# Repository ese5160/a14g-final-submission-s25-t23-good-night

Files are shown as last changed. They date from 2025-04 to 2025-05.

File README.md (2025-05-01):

Review Assignment Due Date (https://classroom.github.com/a/AlBFWSQg)
# a14g-final-submission

    * Team Number: T23
    * Team Name: Good Night
    * Team Members: Haichao Zhao, Zeng Li
    * Github Repository URL: https://github.com/ese5160/a14g-final-submission-s25-t23-good-night
    * Description of test hardware: (development boards, sensors, actuators, laptop + OS, etc) SAMW25, laptop

## 1. Video Presentation

The link to video presentation: [Video Presentation](https://drive.google.com/file/d/199g08DGVsTHXfeQyzWboZk-IfXS3VhQH/view?usp=sharing)

## 2. Project Summary

- Device Description

> We designed a desk electronic car with multiple functions to entertain users within boring working days. It can be controlled by anyone's voice command and task buttons in the web UI.

> What inspired you to do the project? What problem is your device solving?
>> In our daily life, we usually have to sit in the front of desks for multiple hours and sometimes we need to take a break and have some entertainment to make our life more interesting.
>
>> So in order to provide some ways to relax, we designed this desk electronic car. It will accompany with you and interact with you via your voice. Moreover, it can remaind you to take a break by showing LCD animation and led show. Users can play with it to command it to move around.

> How do you use the Internet to augment your device functionality?
>> We use Claude and chatGPT to give us some advice about chip selection and create some helpful code library.

- Device Functionality

> We use WINC1500 chip to do wifi connection and communicate with our MCU. In order to download firmware over the air, we created a virtual machine and uplode our new firmware. MCU can connect to wifi via wifi module and download the new firmware in the VM website and store it in the bootloader. Besides, we use node-red to remotely control our device via MQTT protocal.

> **Sensors:**
>> IMU
>>
>> Microphone
> 
> **Actuators:**
>> LCD
>>
>> Speaker
>>
>> Motor
>
> **Other modules:**
>> 5V module

> Block diagram
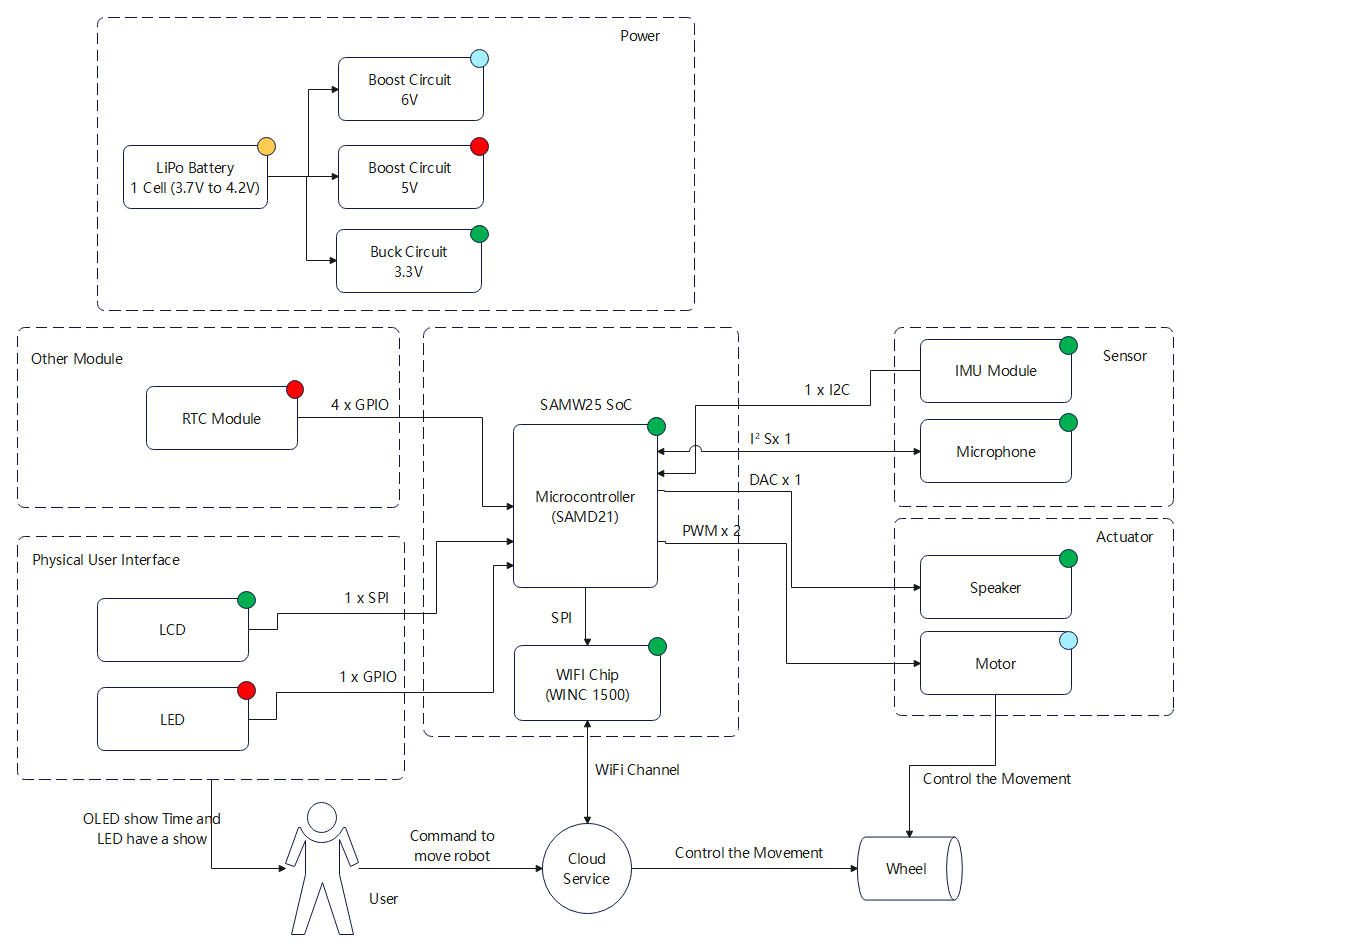
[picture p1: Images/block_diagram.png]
block diagram
> 

- Challenges

> The first great challenge we met is about our 5V power module in our PCBA. The output voltage of 5V module was near 0. So in the end, we chose to desolder the jumpers for the 5V boost and used an individual 5V module and it works.
>
> The second challenge was we connected VSUB net with 5V net directly, which might lead to 5V power supply conflict. So in order to avoid this potential issue, we cut off the copper trace in the PCBA and using fly wire to reconnect the pins between our FTDI chip and power regulator chip. But soldering the fly wires was realy a time-cost and painful process. Luckily, we finished that.
>
> The third challenge is to integrate our individual functions together in FreeRTOS. During the integration process, we found count down time function and health remainder function had a serious conflict and wifi task needed a vary large heap to run successfully. After one whole day debugging, we still cannot integrate the count down time and health remainder together. So we had to give up the count down time function. For the wifi heap allocation, we tried to give smaller heap for each task and give more heap space for wifi. And ultimately, it works.

- Prototype Learnings

> The lessons I have learned from building and testing our prototype:
>> Firstly, deviding VUSB net from 5V boost output net.
>>
>> Secondly, always double even trible check the components to make sure their standard running voltage and current and power.
>>
>> Thirdly, when choosing LED strip, I need to figure out whether the MCU can provide the clock freqency required by the LED strip.

> What would you do differently if you had to build this device again?
> 
> I will definitely check my key components standard working condition such as inductors used for power regulator. And split the VUSB with 5V net.
 
- Next Steps & Takeaways

> What steps are needed to finish or improve this project?
>> We need to improve our UI display to show IMU data and configure our RTC initial time via Node-Red rather than software setup. Beside we need to add a distance sensor to detect the surrounding item in order to avoid falling from high altitude.

> What did you learn in ESE5160 through the lectures, assignments, and this course-long prototyping project?
>> Lots of things, including:
>> - Altium Designer using
>> - The procedure of PCBA designing
>> - PCBA test procedure
>> - Advanced soldering skills
>> - Professional device using: scrimper, e-load, temperature test gun, etc.
>> - MQTT based IOT controlling.
>> - Node-Red using
>> - OTAFU implementing
>> - FreeRTOS utilizing
>> - etc

- Project Links
> [URL to your Node-RED instance for our review ](http://172.177.231.136:1880/ui/#!/0?socketid=XXV4ffUuj0cg4lLcAAEU)

> [The share link to your final PCBA on Altium 365.](https://upenn-eselabs.365.altium.com/designs/7828C69B-F65F-46A7-A406-FC1A5B1ED7EE)

## 3. Hardware & Software Requirements

**Pass**:

- [√] Design Review Criteria

**Fail**:

- [ ] Design Review Criteria

### For Hardware Requirements

- [√] Project shall be based on SAMW25 microcontroller.

- [√] A 39x41x3.3mm OLED shall be used as user interface.

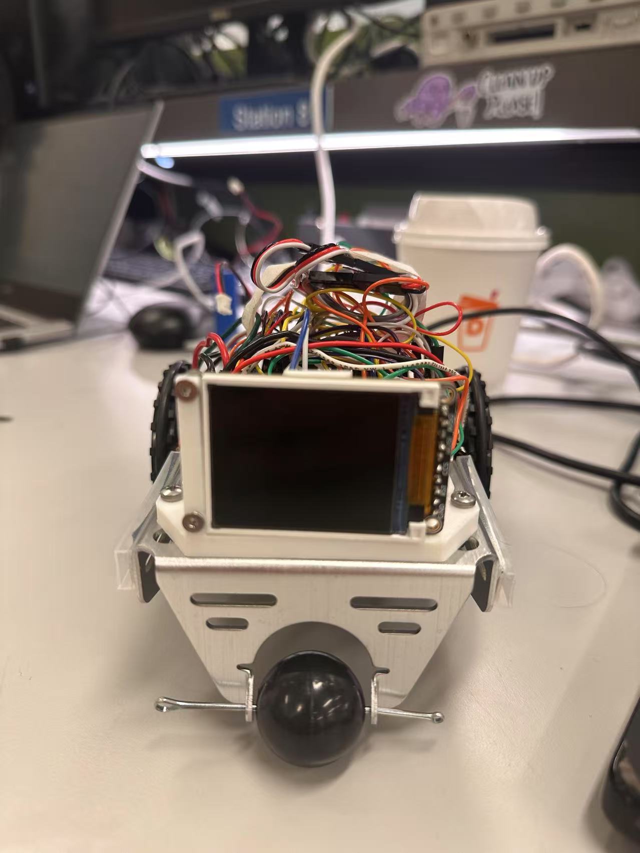
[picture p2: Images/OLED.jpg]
OLED


- [√] The Electronic Pet shall move around with wheels controlled by PWM signals(≥20kHz frequency).

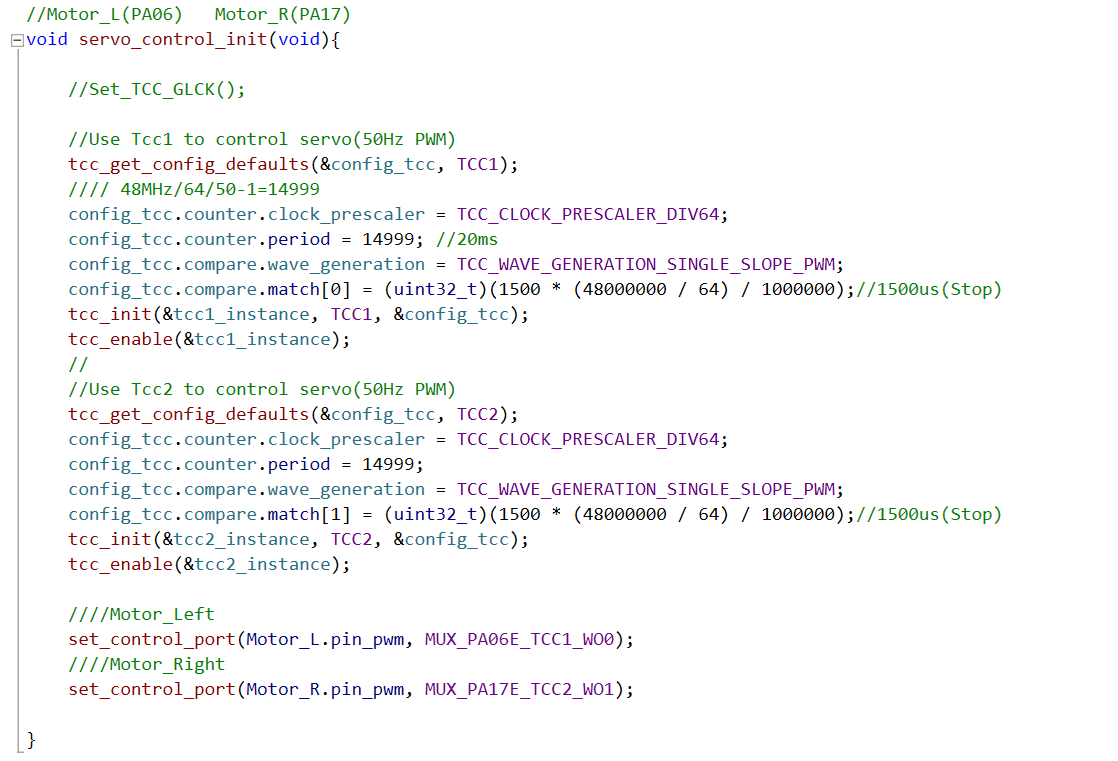
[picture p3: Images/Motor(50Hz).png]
PWM Signals


- [√] The project shall utilize a microphone to capture users' voice command.

[Voice Command](https://drive.google.com/file/d/1vsd7IJbTeATzNU7q7ol-T68C_iqhJChO/view?usp=sharing)

- [√] The project shall utilize a speaker to play audio signals.

[Audio Signals](https://drive.google.com/file/d/1vsd7IJbTeATzNU7q7ol-T68C_iqhJChO/view?usp=sharing)

- [√] The Electronic Pet shall have colorful lightning effect by using led strips based on I/O pins sending color data.

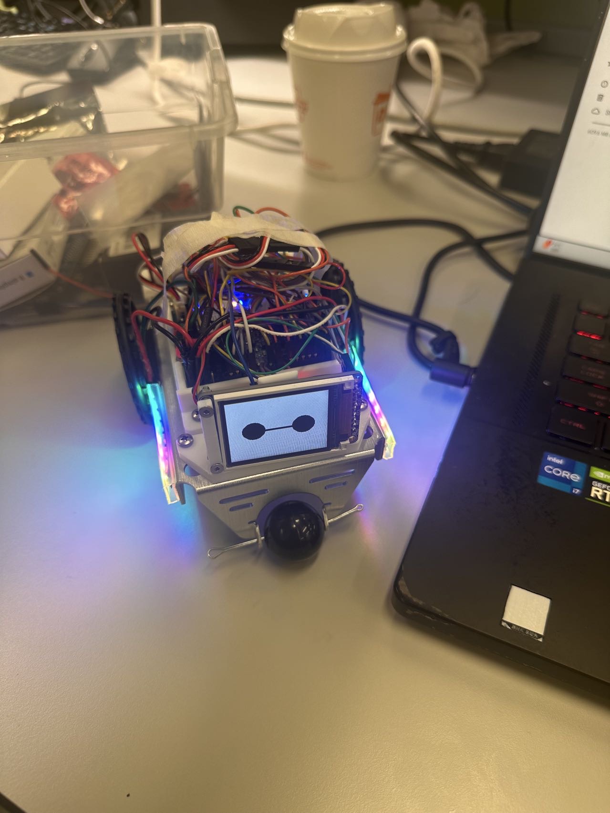
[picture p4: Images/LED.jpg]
LED Strip


- [√] The Electronic Pet shall using 1-cell Li-Po battery with normal voltage 3.7V to power itself.

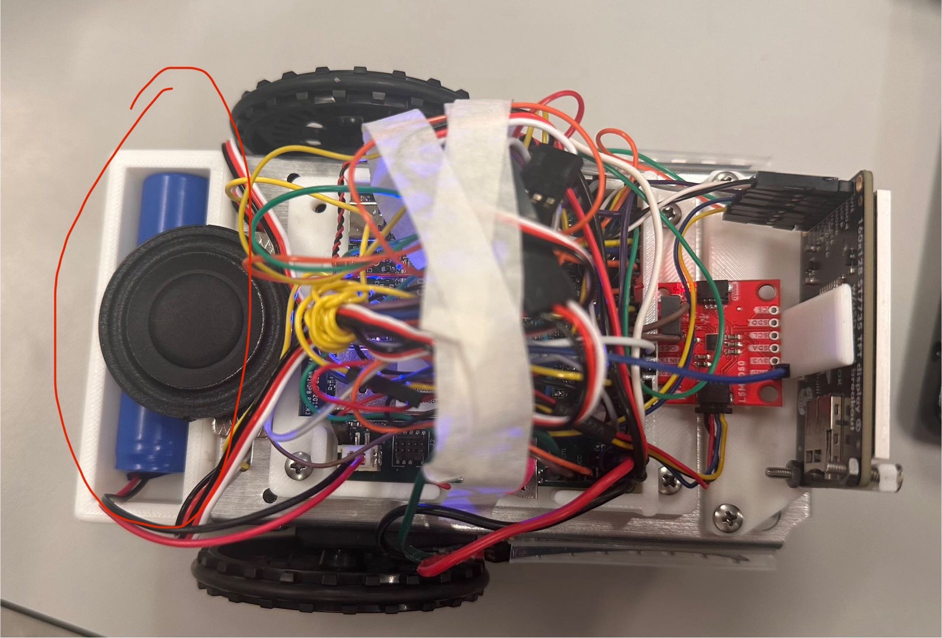
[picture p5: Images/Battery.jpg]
Battery


- [ ] The Elctronic Pet shall have a hardware audio weak-up button to activate voice detection functionality.

(But for this one, we can weak-up audio by using voice command)

[Voice Weak-up](https://drive.google.com/file/d/1QjdPzAFBdYn6xlC-yM1D15jq5Nro2u9h/view?usp=drive_link)

- [√] The Elctronic Pet shall have a switch to allow firmware downloaded between MCU and AI voice module.

- [√] The Elctronic Pet shall have a reset button to reset MCU.

### For Software Requirements

- [√] The OLED shall show real time clock with time changing animation under idle mode.

[Real Time Clock](https://drive.google.com/file/d/113563IdeDLPqgcDlNYIJI8t_Kfd6H3IC/view?usp=sharing)

- [√] The Electronic Pet shall count down time, set by users' voice command(all voice ommand response time ≤100ms and all voice recognition accuracy ≥95%).

[Voice Control](https://drive.google.com/file/d/1uEhCCXdXMqlJPuAjUW_ZJtCygNJ_ypcy/view?usp=drive_link)

- [√] The OLED shall show time counting down changing animation.

[Count Down Time](https://drive.google.com/file/d/1uEhCCXdXMqlJPuAjUW_ZJtCygNJ_ypcy/view?usp=drive_link)

- [√] The project shall control LED strip to display several modes: blinking with one color in 0.5 milisecond period, holding in one color, holding in multiple colors.

[Led Modes](https://drive.google.com/file/d/1Ynfru8uWko6rZNohwsRf4ItYq9wje_we/view?usp=drive_link)

- [√] The Electronic Pet shall move forward, move backward, turn left and turn right based on users' voice command or mobile application control.

[Motor Control Based on Node-RED](https://drive.google.com/file/d/1fZCSuxt042b5PfyyEALYGmumLY5jCH-g/view?usp=sharing)

[Motor Control Based on Voice Module](https://drive.google.com/file/d/1cLYKxjtBCbKXMLHO_yQR-n1LWBqkUQFy/view?usp=sharing)

- [√] The Electronic Pet shall remind users to take breaks (OLED displaying animation for 10 seconds) and play a light show when 30 minutes counting down ends. (For test, we set time to 60 seconds)

[Health Reminder](https://drive.google.com/file/d/1pByXs5zT0Y9-n48iyKIn96K74kvmEg7N/view?usp=sharing)

- [√] The Electronic Pet shall recognize and answer users' voice commands in 3 seconds after recieving voice activation commands.

[Voice Command Answer in 3 seconds](https://drive.google.com/file/d/1vsd7IJbTeATzNU7q7ol-T68C_iqhJChO/view?usp=sharing)

- [√] The OLED display shall communicate with MCU via SPI bus(≥10MHz) and display refresh rate ≥30fps.

- [√] The microphone shall send signals to AI module via I2S bus(Audio sampling rate ≥44.1kHz).

- [√] The speaker shall communicate with AI module via PWM/DAC signals.

## 4. Project Photos & Screenshots

- Final project, including any casework or interfacing elements that make up the full project (3D prints, screens, buttons, etc)

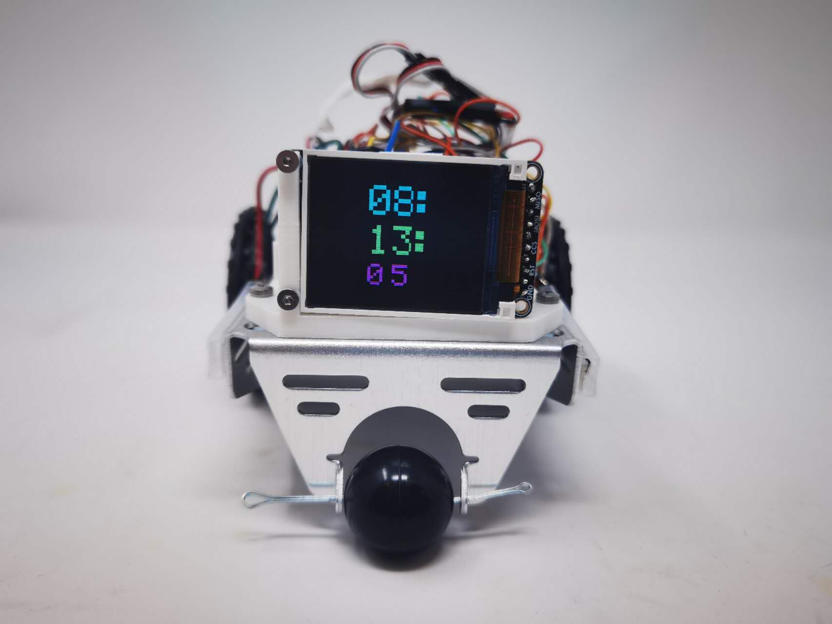
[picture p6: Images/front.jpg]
front

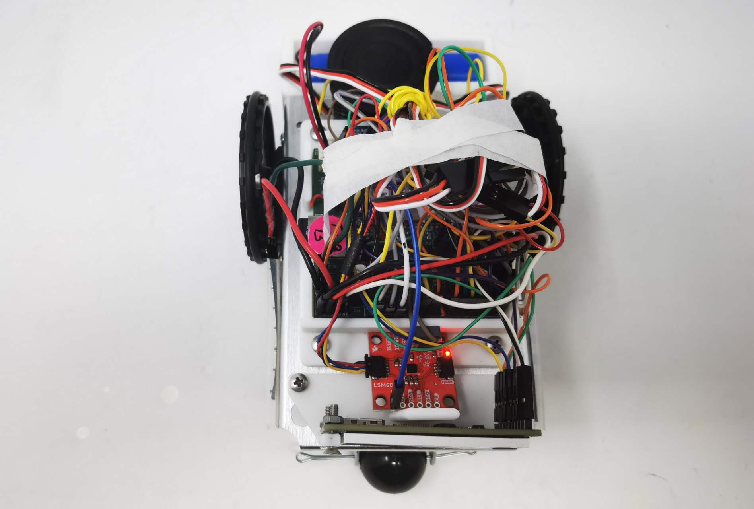
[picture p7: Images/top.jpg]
top

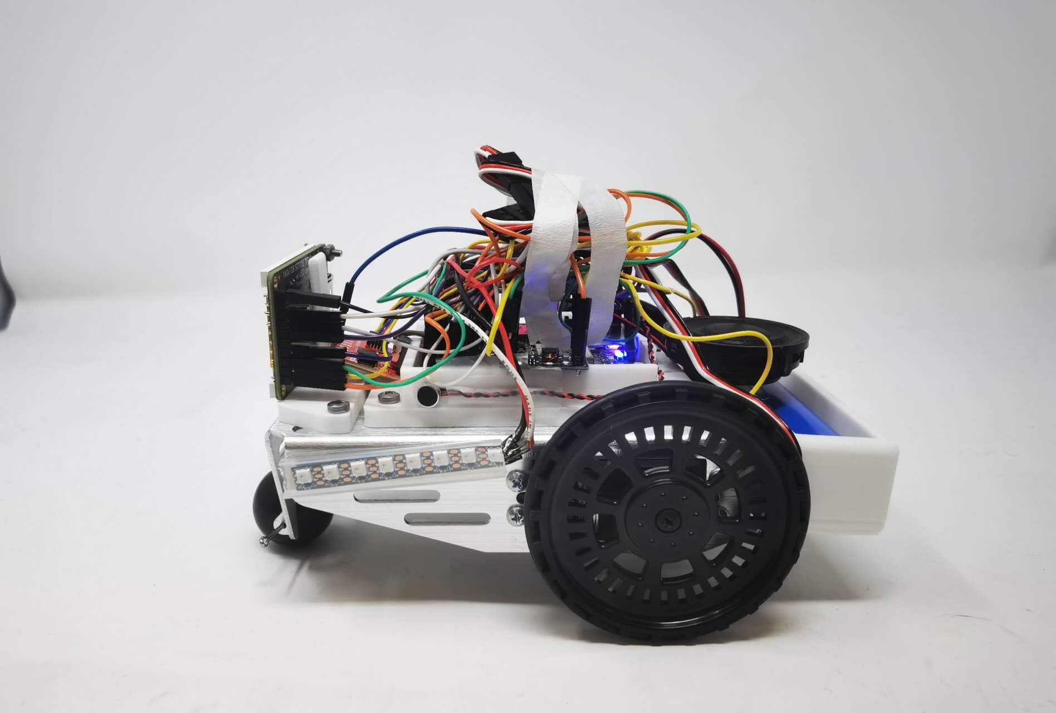
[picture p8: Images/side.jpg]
side

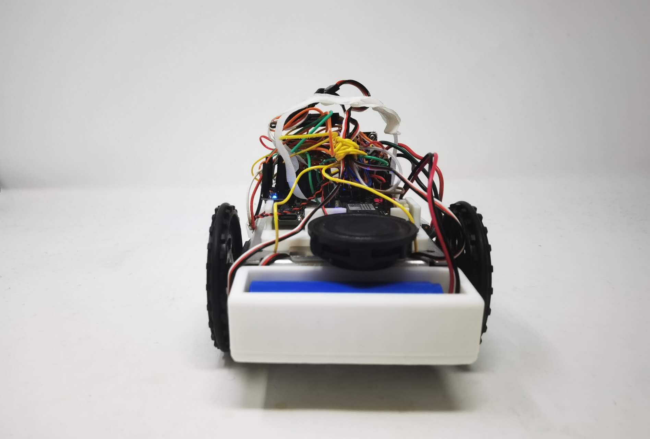
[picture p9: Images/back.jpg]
back

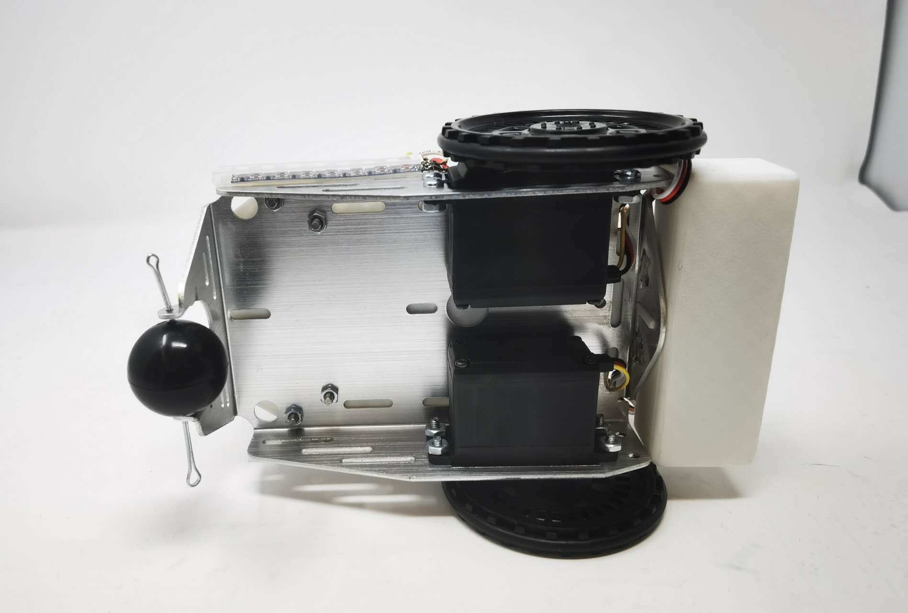
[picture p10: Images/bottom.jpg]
bottom


- The standalone PCBA, top
The standalone PCBA, top
- The standalone PCBA, bottom
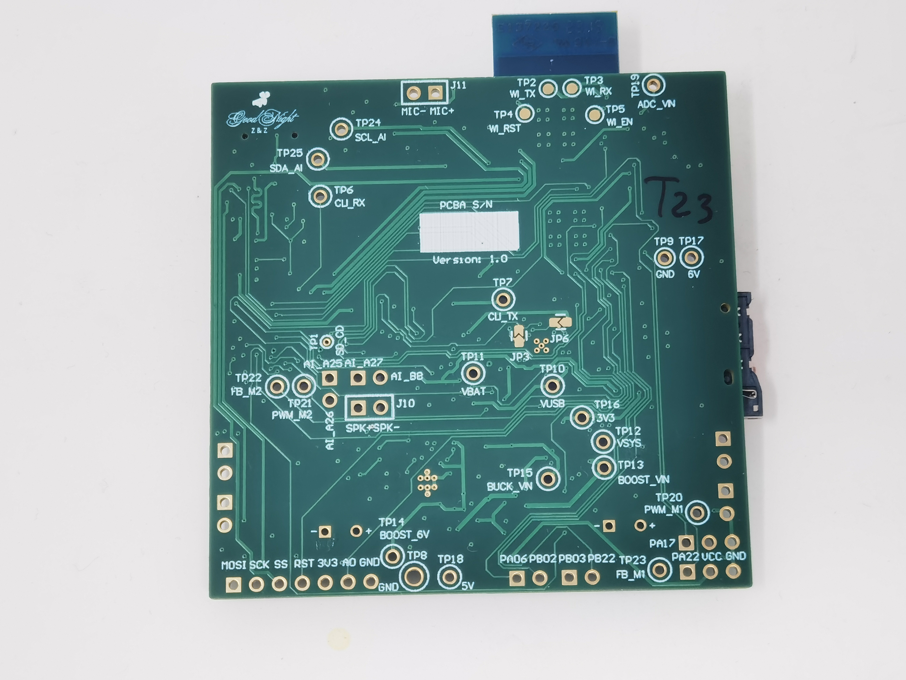
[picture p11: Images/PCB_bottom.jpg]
The standalone PCBA, bottom

- Thermal camera images while the board is running under load 
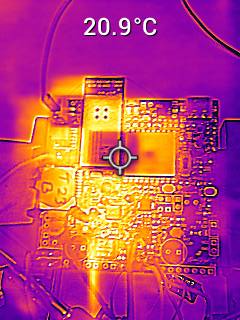
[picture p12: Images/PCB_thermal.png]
Thermal camera images

- The Altium Board design in 2D view (screenshot)
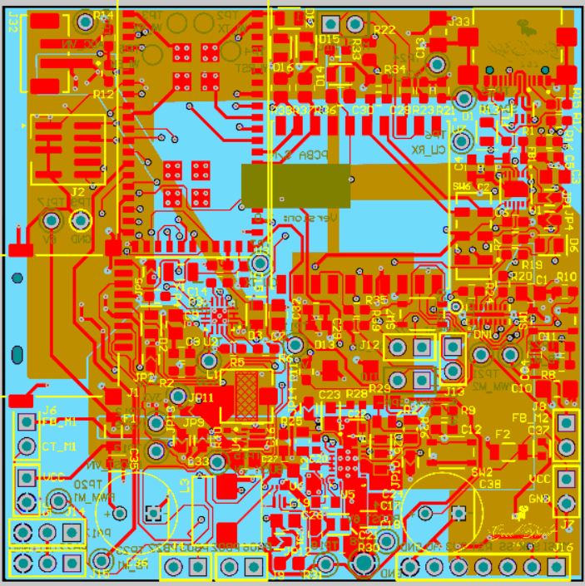
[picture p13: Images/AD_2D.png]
AD_2D

- The Altium Board design in 3D view (screenshot)
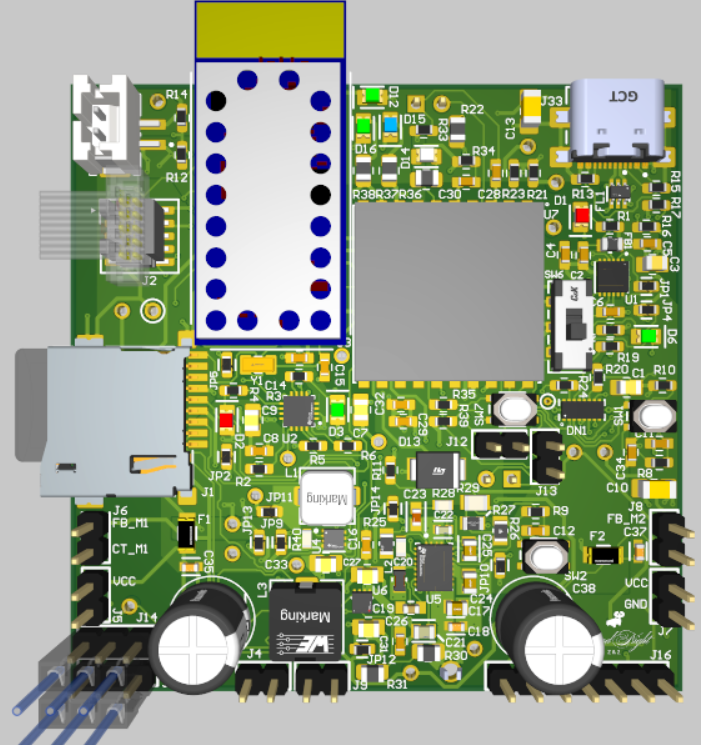
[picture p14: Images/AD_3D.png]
AD_3D

- Node-RED dashboard (screenshot)
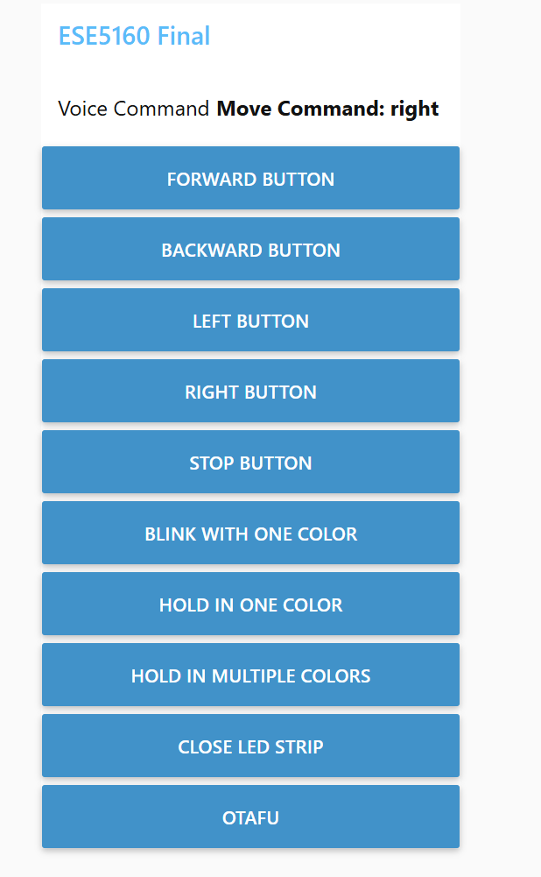
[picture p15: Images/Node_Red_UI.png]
UI

- Node-RED backend (screenshot)
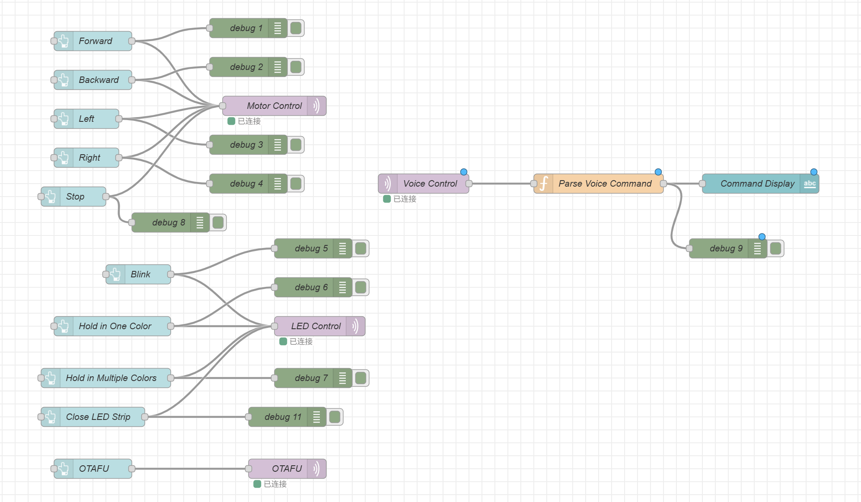
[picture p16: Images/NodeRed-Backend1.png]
backend_1

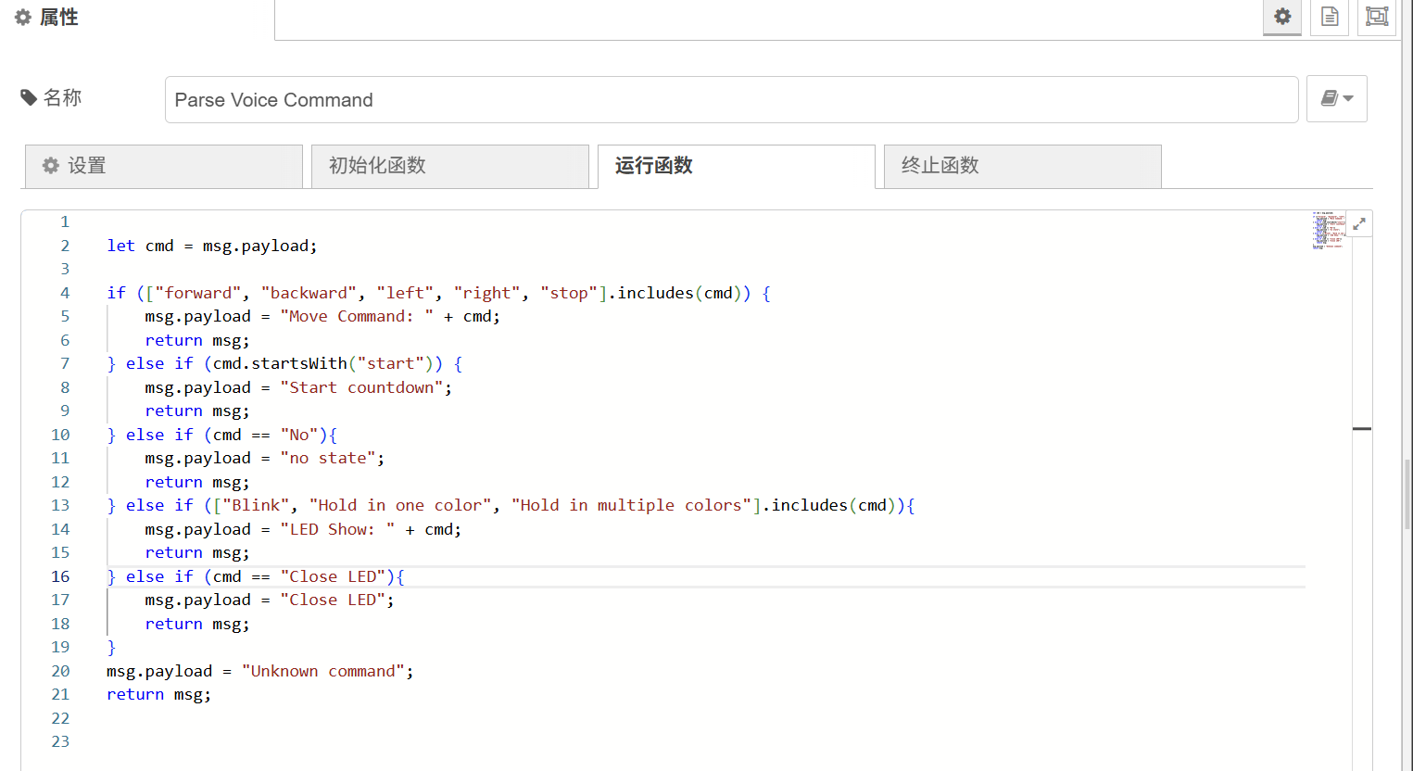
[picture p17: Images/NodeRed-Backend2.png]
backend_2

- Block diagram of your system
block diagram

## Codebase

- [Link to our final embedded C application firmware codebases](https://github.com/ese5160/a14g-final-submission-s25-t23-good-night/tree/main/Application)

- [Link to our final embedded C bootloader firmware codebases](https://github.com/ese5160/a14g-final-submission-s25-t23-good-night/tree/main/Bootloader)

- [Link to our AI voice module code](uni_hb_m_solution.zip)

- [Link to our Node-RED dashboard code](node_red.json)

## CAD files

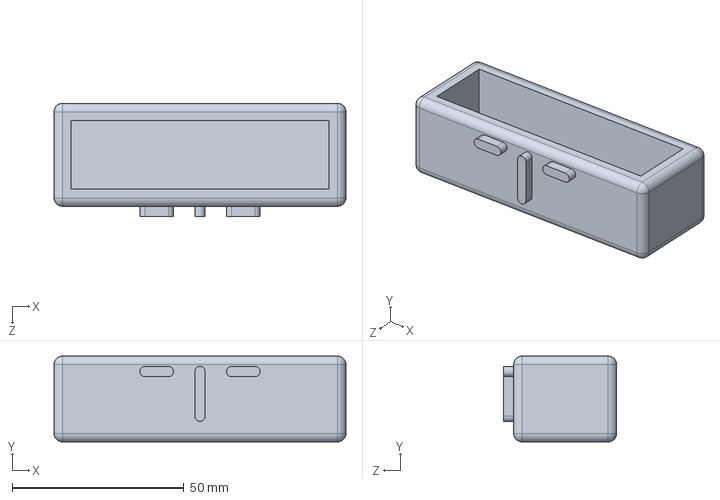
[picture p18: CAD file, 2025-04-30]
3D_Model/battery_cage.SLDPRT
85.0 x 25.0 x 33.0 mm

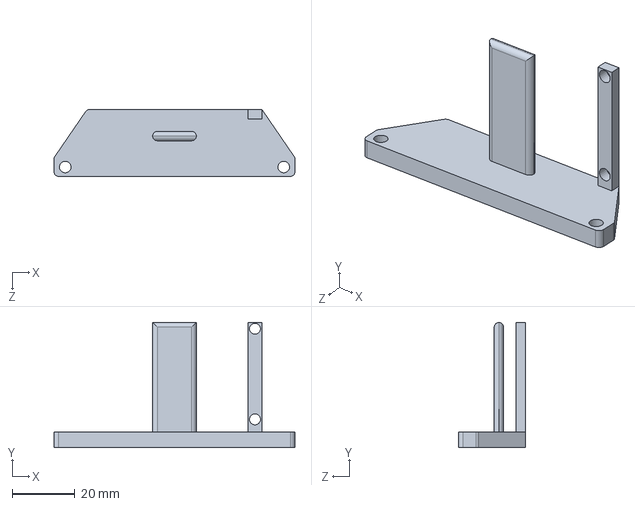
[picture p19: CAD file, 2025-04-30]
3D_Model/LCD_base.SLDPRT
77.1 x 40.0 x 21.4 mm

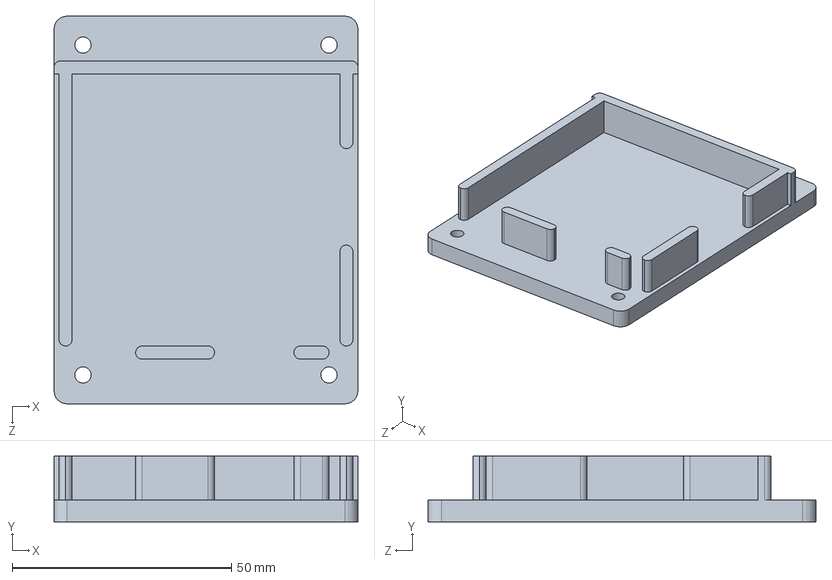
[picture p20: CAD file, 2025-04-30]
3D_Model/base.SLDPRT
69.3 x 15.0 x 88.4 mm

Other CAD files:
3D_Model/LCD_base.STL
3D_Model/base.STL
3D_Model/battery_cage.STL

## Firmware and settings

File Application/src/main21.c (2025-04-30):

/**
 * @file      main.c
 * @brief     Main application entry point
 * @author    Eduardo Garcia
 * @author    Nick M-G
 * @date      2022-04-14
 ******************************************************************************/

/****
 * Includes
 ******************************************************************************/
#include <errno.h>

#include "CliThread/CliThread.h"
#include "FreeRTOS.h"
#include "I2cDriver\I2cDriver.h"
#include "SerialConsole.h"
#include "WifiHandlerThread/WifiHandler.h"
#include "asf.h"
#include "driver/include/m2m_wifi.h"
#include "main.h"
#include "stdio_serial.h"

#include "Motor.h"
#include "LCD/LCD.h"
#include "RTC_LCD/rtc_lcd.h"
#include "LED/LED.h"
#include "Health_Reminder/Health_Reminder.h"
#include "AI_voice_control/voice_control.h"
#include "IMU/lsm6dso_reg.h"
#include "IMU/ImuTask.h"

#include "flag.h"

/****
 * Defines and Types
 ******************************************************************************/
#define APP_TASK_ID 0 /**< @brief ID for the application task */
#define CLI_TASK_ID 1 /**< @brief ID for the command line interface task */
#define WAIT_TX_COMPLETE_MS 1000

/****
 * Local Function Declaration
 ******************************************************************************/
void vApplicationIdleHook(void);
//!< Initial task used to initialize HW before other tasks are initialized
static void StartTasks(void);
void vApplicationDaemonTaskStartupHook(void);

void vApplicationStackOverflowHook(void);
void vApplicationMallocFailedHook(void);
void vApplicationTickHook(void);

/****
 * Variables
 ******************************************************************************/
static TaskHandle_t cliTaskHandle = NULL;       //!< CLI task handle
static TaskHandle_t daemonTaskHandle = NULL;    //!< Daemon task handle
static TaskHandle_t wifiTaskHandle = NULL;      //!< Wifi task handle
static TaskHandle_t uiTaskHandle = NULL;        //!< UI task handle
static TaskHandle_t controlTaskHandle = NULL;   //!< Control task handle
static TaskHandle_t healthTaskHandle = NULL;    //!< Health Monitor task handle
static TaskHandle_t lcdTaskHandle = NULL;		//!< LCD task handle
static TaskHandle_t ledTaskHandle = NULL;		//!< LED task handle
static TaskHandle_t voicecontrolTaskHandle = NULL;//!< Voice Control task Handle
static TaskHandle_t imuTaskHandle = NULL;

char bufferPrint[64];   ///< Buffer for daemon task

SystemState system_state = counting_down;

SemaphoreHandle_t xHealthMonitorSemaphore = NULL; // For Health Monitor

volatile int stop_rtc_show_flag = 0;
volatile int led_flag = 0;
volatile bool health_monitor_flag = false;
volatile bool stop_all_flag = false;
volatile int rtc_mode = 0;
volatile int voice_control_flag = 11; //0 is no task   11 for test    12 nothing

volatile rtc_time_t current_time;

/**
 * @brief Main application function.
 * Application entry point.
 * @return int
 */
int main(void) {
    /* Initialize the board. */
    system_init();
	SK6812_Init();
	configure_tcc0();
	servo_control_init();
	delay_init();	
	Command_Detect();
    // Initialize trace capabilities
    vTraceEnable(TRC_START);
    // Start FreeRTOS scheduler
    vTaskStartScheduler();
	
	
    return 0;   // Will not get here
}

/**
 * function          vApplicationDaemonTaskStartupHook
 * @brief            Initialization code for all subsystems that require FreeRToS
 * @details			This function is called from the FreeRToS timer task. Any code
 *					here will be called before other tasks are initilized.
 * @param[in]        None
 * @return           None
 */
void vApplicationDaemonTaskStartupHook(void) {
	InitializeSerialConsole();
    SerialConsoleWriteString("\r\n\r\n-----ESE516 Main Program-----\r\n");

     //Initialize HW that needs FreeRTOS Initialization
    SerialConsoleWriteString("\r\n\r\nInitialize HW...\r\n");
    if (I2cInitializeDriver() != STATUS_OK) {
	    SerialConsoleWriteString("Error initializing I2C Driver!\r\n");
	    } else {
	    SerialConsoleWriteString("Initialized I2C Driver!\r\n");
    }
	//I2CScanBus();
	xHealthMonitorSemaphore = xSemaphoreCreateBinary();
	if (xHealthMonitorSemaphore == NULL) {
		SerialConsoleWriteString("ERR: Failed to create HealthMonitorsemaphore!\r\n");
	}
	
	
    StartTasks();

    vTaskSuspend(daemonTaskHandle);
}

/**
 * function          StartTasks
 * @brief            Initialize application tasks
 * @details
 * @param[in]        None
 * @return           None
 */
static void StartTasks(void) {
    snprintf(bufferPrint, 64, "Heap before starting tasks: %d\r\n", xPortGetFreeHeapSize());
    SerialConsoleWriteString(bufferPrint);

    // Initialize Tasks here (Change Stack Size)
	
	//CLI Task
    if (xTaskCreate(vCommandConsoleTask, "CLI_TASK", CLI_TASK_SIZE, NULL, CLI_PRIORITY, &cliTaskHandle) != pdPASS) {
        SerialConsoleWriteString("ERR: CLI task could not be initialized!\r\n");
    }

    snprintf(bufferPrint, 64, "Heap after starting CLI: %d\r\n", xPortGetFreeHeapSize());
    SerialConsoleWriteString(bufferPrint);
	
	////LCD Task(1200 -> 512 -> 256)
	if (xTaskCreate(rtc_lcd_display_task, "LCD_TASK", 512-128, NULL, 4, &lcdTaskHandle) != pdPASS) {
		SerialConsoleWriteString("ERROR: LCD task could not be initialized!\r\n");
		} else {
		SerialConsoleWriteString("LCD task created successfully\r\n");
	}
	snprintf(bufferPrint, 64, "Heap after starting LCD: %d\r\n", xPortGetFreeHeapSize());
	SerialConsoleWriteString(bufferPrint);

	////Health Monitor Task
	if (xTaskCreate(vHealthMonitorTask, "Health_Monitor_TASK", 128, NULL, 3, &healthTaskHandle) != pdPASS) {
		SerialConsoleWriteString("ERR: Health Monitor task could not be initialized!\r\n");
	}
	snprintf(bufferPrint, 64, "Heap after starting Health Monitor: %d\r\n", xPortGetFreeHeapSize());
	SerialConsoleWriteString(bufferPrint);

	//WIFI Task(1024 -> 512)
	if (xTaskCreate(vWifiTask, "WIFI_TASK", 1024-128, NULL, WIFI_PRIORITY, &wifiTaskHandle) != pdPASS) {
		SerialConsoleWriteString("ERR: WIFI task could not be initialized!\r\n");
	}
	snprintf(bufferPrint, 64, "Heap after starting WIFI: %d\r\n", xPortGetFreeHeapSize());
	SerialConsoleWriteString(bufferPrint);

	////////Voice Control Task
	if (xTaskCreate(vVoiceControlTask, "Voice_Control_TASK", 128, NULL, 3, &voicecontrolTaskHandle) != pdPASS) {
		SerialConsoleWriteString("ERR: Voice Control task could not be initialized!\r\n");
	}
	snprintf(bufferPrint, 64, "Heap after starting Voice Control: %d\r\n", xPortGetFreeHeapSize());
	SerialConsoleWriteString(bufferPrint);
	
	//////IMU
	if (xTaskCreate(vIMUTask, "IMU_TASK", 128, NULL, 3, &imuTaskHandle) != pdPASS) {
		SerialConsoleWriteString("ERR: IMU Initialization Failed£¡\r\n");
		} else {
		SerialConsoleWriteString("IMU Created Successfully\r\n");
	}
	snprintf(bufferPrint, 64, "Heap after starting IMU: %d\r\n", xPortGetFreeHeapSize());
	SerialConsoleWriteString(bufferPrint);
	


//LED Task(512 -> 256)
	if (xTaskCreate(LED_Task, "LED_TASK", 128, NULL, 3, &ledTaskHandle) != pdPASS) {
		SerialConsoleWriteString("ERR: LED Initialization Failed£¡\r\n");
		} else {
		SerialConsoleWriteString("LED Created Successfully\r\n");
	}
	snprintf(bufferPrint, 64, "Heap after starting LED: %d\r\n", xPortGetFreeHeapSize());
	SerialConsoleWriteString(bufferPrint);
}

void vApplicationMallocFailedHook(void) {
    SerialConsoleWriteString("Error on memory allocation on FREERTOS!\r\n");
    while (1)
        ;
}

void vApplicationStackOverflowHook(void) {
    SerialConsoleWriteString("Error on stack overflow on FREERTOS!\r\n");
    while (1)
        ;
}

#include "MCHP_ATWx.h"
void vApplicationTickHook(void) { SysTick_Handler_MQTT(); }

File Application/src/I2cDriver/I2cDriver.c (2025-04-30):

/**************************************************************************/ /**
 * @file      I2cDriver.c
 * @brief     FreeRTOS compatible driver for I2C communications
 * @author    Eduardo Garcia
 * @date      2020-04-05

 ******************************************************************************/

/******************************************************************************
 * Includes
 ******************************************************************************/
#include "I2cDriver.h"

/******************************************************************************
 * Defines
 ******************************************************************************/

/******************************************************************************
 * Variables
 ******************************************************************************/
SemaphoreHandle_t sensorI2cMutexHandle;                       ///< Mutex to handle the sensor I2C bus thread access.
SemaphoreHandle_t sensorI2cSemaphoreHandle;                   ///< Binary semaphore to notify task that we have received an I2C interrupt on the Sensor bus
static volatile TaskHandle_t xTaskToNotifySensorDone = NULL;  ///< Stores the handle of the task that will be notified when the SENSOR transmission is complete. */
static uint8_t sensorTransmitError = false;                   ///< Flag used to indicate that there was an I2C transmission error on the SENSOR bus.

struct i2c_master_module i2cSensorBusInstance;
static I2C_Bus_State I2cSensorBusState;  ///< Structure that defines the I2C Bus used for the sensors.

struct i2c_master_packet sensorPacketWrite;
/******************************************************************************
 * Forward Declarations
 ******************************************************************************/
static int32_t I2cDriverConfigureSensorBus(void)
{
    int32_t error = STATUS_OK;
    status_code_genare_t errCodeAsf = STATUS_OK;
    /* Initialize config structure and software module */
    struct i2c_master_config config_i2c_master;
    i2c_master_get_config_defaults(&config_i2c_master);

    config_i2c_master.pinmux_pad0 = PINMUX_PA04D_SERCOM0_PAD0;//PINMUX_PA08C_SERCOM0_PAD0;//
    config_i2c_master.pinmux_pad1 = PINMUX_PA05D_SERCOM0_PAD1;//PINMUX_PA09C_SERCOM0_PAD1;//
    /* Change buffer timeout to something longer */
    config_i2c_master.buffer_timeout = 1000;
    /* Initialize and enable device with config. Try three times to initialize */

    for (uint8_t i = I2C_INIT_ATTEMPTS; i != 0; i--) {
        errCodeAsf = i2c_master_init(&i2cSensorBusInstance, SERCOM0, &config_i2c_master);
        if (STATUS_OK == errCodeAsf) {
            error = errCodeAsf;
            break;
        } else {
            i2c_master_reset(&i2cSensorBusInstance);
        }
    }

    if (STATUS_OK != error) goto exit;

    i2c_master_enable(&i2cSensorBusInstance);

exit:
    return error;
}
/******************************************************************************
 * Callback Functions
 ******************************************************************************/
/*
  * @fn			void I2cSensorsTxComplete(struct i2c_m_async_desc *const i2c)
  * @brief       Callback function for when the SENSORS I2C bus ends transmissions
  * @details     This callback sets a flag that tells us that the bus is not busy, and the last transmission is done. With USE_FREERTOS flag, this
                                 callback notifies the registered thread that the I2C transfer has finished. The registered thread is the thread that initiated the I2C transaction,
                                 and is currently waiting for a notification that it has finished.
  * @param[in]   i2c Pointer to I2C structure used inside the Atmel ASFv3  framework
  * @return      This function is a callback, and it is registered as such when we send an I2C transmission on this I2C bus.
  * @note
  */
void I2cSensorsTxComplete(struct i2c_master_module *const module)
{
    I2cSensorBusState.i2cState = I2C_BUS_READY;
    I2cSensorBusState.rxDoneFlag = true;
    BaseType_t xHigherPriorityTaskWoken = pdFALSE;

    xSemaphoreGiveFromISR(sensorI2cSemaphoreHandle, &xHigherPriorityTaskWoken);
    sensorTransmitError = false;
    portYIELD_FROM_ISR(xHigherPriorityTaskWoken);
}

/**
  * @fn				void I2cSensorRxComplete(struct i2c_m_async_desc *const i2c)
  * @brief			Callback function for when the SENSOR I2C bus ends data reception
  * @details			This callback sets a flag that tells us that the bus is not busy, and the last reception is done. With USE_FREERTOS flag, this
                                         callback notifies the registered thread that the I2C transfer has finished. The registered thread is the thread that initiated the I2C transaction,
                                         and is currently waiting for a notification that it has finished.
  * @param[in]		i2c Pointer to I2C structure used inside the Atmel ASFv3  framework
  * @return			This function is a callback, and it is registered as such when we send an I2C reception on this I2C bus.
  * @note
  */
void I2cSensorsRxComplete(struct i2c_master_module *const module)
{
    I2cSensorBusState.i2cState = I2C_BUS_READY;
    I2cSensorBusState.rxDoneFlag = true;
    BaseType_t xHigherPriorityTaskWoken = pdFALSE;

    xSemaphoreGiveFromISR(sensorI2cSemaphoreHandle, &xHigherPriorityTaskWoken);
    sensorTransmitError = false;
    portYIELD_FROM_ISR(xHigherPriorityTaskWoken);
}

/**
  * @fn				void I2cSensorError(struct i2c_m_async_desc *const i2c)
  * @brief			Callback function for when the LED I2C bus encounters an error while transmitting/receiving
  * @details			This callback sets a flag that tells us that the bus is not busy, and the last reception is done. With USE_FREERTOS flag, this
                                         callback notifies the registered thread that the I2C transfer has finished. The registered thread is the thread that initiated the I2C transaction,
                                         and is currently waiting for a notification that it has finished.
  * @param[in]		i2c Pointer to I2C structure used inside the Atmel ASFv3  framework
  * @return			This function is a callback, and it is registered as such when we send an I2C reception on this I2C bus.
  * @note
  */
void I2cSensorsError(struct i2c_master_module *const module)
{
    I2cSensorBusState.i2cState = I2C_BUS_READY;
    I2cSensorBusState.txDoneFlag = true;
    BaseType_t xHigherPriorityTaskWoken = pdFALSE;

    xSemaphoreGiveFromISR(sensorI2cSemaphoreHandle, &xHigherPriorityTaskWoken);
    sensorTransmitError = true;
    portYIELD_FROM_ISR(xHigherPriorityTaskWoken);
}
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

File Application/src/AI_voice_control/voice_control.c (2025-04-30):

/*
 * voice_control.c
 *
 * Created: 2025-04-26 23:32:51
 *  Author: 13356
 */ 
#include "voice_control.h"

#define VC02_I2C_ADDRESS 0x28
#define VC02_CMD_REG     0x01
#define I2C_TIMEOUT      pdMS_TO_TICKS(200)

#define PORT1 PIN_PA03 //CTRL M1      Voice Module A25
#define PORT2 PIN_PA02 //CTRL M2	  Voice Module A26
#define PORT3 PIN_PA20 // FB 2		  Voice Module A27
#define PORT4 PIN_PA10 //VBatin		  Voice Module B8

void set_output(uint32_t port){
	struct port_config pin_conf;
	port_get_config_defaults(&pin_conf);
	pin_conf.direction = PORT_PIN_DIR_INPUT;
	port_pin_set_config(port, &pin_conf);
}
	

void Command_Detect(void){
	set_output(PORT1);
	set_output(PORT2);
	set_output(PORT3);
	set_output(PORT4);

}

/*
flag = 0 -> No State(Idle Task)
flag = 4 -> Count down time
flag = 1 -> LED show(Blink)
flag = 2 -> LED show(Hold in one color)
flag = 3 -> LED show(Hold in multiple color)
flag = 5 -> Motor(Move forward)
flag = 6 -> Motor(Move backward)
flag = 7 -> Motor(Move leftward)
flag = 8 -> Motor(Move rightward)
flag = 9 -> Motor(Stop)
flag = 10-> CLear all state and return to no state
***********************************************************************/
void vVoiceControlTask(void *pvParameters){
	while(1){
		static int pre_voice_flag = 50;
		uint8_t a = port_pin_get_input_level(PORT1);
		uint8_t b = port_pin_get_input_level(PORT2);
		uint8_t c = port_pin_get_input_level(PORT3);
		uint8_t d = port_pin_get_input_level(PORT4);
		voice_control_flag = 8*d + 4*c + 2*b + a;
		if(voice_control_flag != pre_voice_flag){		
			if (voice_control_flag == 0){}
			else if (voice_control_flag == 1 ){
				//BLink_one_color();
				led_flag = 1;
			}
			else if (voice_control_flag == 2){
				//Hold_in_one_color();
				led_flag = 2;
			}
			else if (voice_control_flag == 3){
				//rainbow_swirl();
				led_flag = 3;
			}		
			else if (voice_control_flag == 4){
				//SK6812_Clear();
				led_flag = 4;
			}
			else if (voice_control_flag == 5){
				counting_down_time();
			}
			else if (voice_control_flag == 6){
				move_forward();
			}
			else if (voice_control_flag == 7){
				move_backward();
			}
			else if (voice_control_flag == 8){
				move_left();
			}
			else if (voice_control_flag == 9){
				move_right();
			}										
			else if (voice_control_flag == 10){
				stop();
			}
			else if (voice_control_flag == 11){//Clear All state and return
				//stop_all_flag = true;
				stop();
				SK6812_Clear();
				voice_control_flag = 0;
			}
			else if (voice_control_flag == 12){//For Test£©
				vTaskDelay(5000);
				voice_control_flag = 6;
			}
			//else if (voice_control_flag == 15){
				//PM->RCAUSE.reg = PM_RCAUSE_SYST;
			//}
		pre_voice_flag = voice_control_flag;
		vTaskDelay(pdMS_TO_TICKS(1000)); 
		}
	
	}

}
//
